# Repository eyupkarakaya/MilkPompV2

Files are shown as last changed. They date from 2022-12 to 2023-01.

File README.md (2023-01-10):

# Milk Pomp
Proje, kullanicinin farkli tip ve hacimli bardaklara makineden süt doldurmak için kullanilacak bir cihazin kontrol kartinin tasarlanmasi işidir.

Cihazın mekanik tasarımı, flow sensör ve pompa seçimi müşteri tarafından hazırlanmıştır. Bizim yapacağımız iş ise sistemin çalışmasını sağlayacak elektronik kontrol kartının tasarlanmasıdır.

## Sistemin Çalismasi
Cihaz maksimum 9 farklı bardak bilgisini hafızada tutabilir. Kullanıcı bardak seçimi yaparak kayıtlı bardak tiplerinden birini otomatik olarak doldurabilir. Fakat istenirse kayıtlı olmayan farklı bir kabı da manuel olarak istediği miktarda doldurabilir.

Cihaz üzerinde 3 adet buton ve 1 adet 7-Segment gösterge bulunmaktadır. Ayrıca, bir pulse girişi ile **Akış Sensoru** girişi okunacak ve çıkış olarak bir role kontrol edilecektir.

	* I/O (On/Off) butonu
	* Start butonu
	* Mode butonu
	* Akış Sensoru (Encoder Pulse Input)
	* Role
	
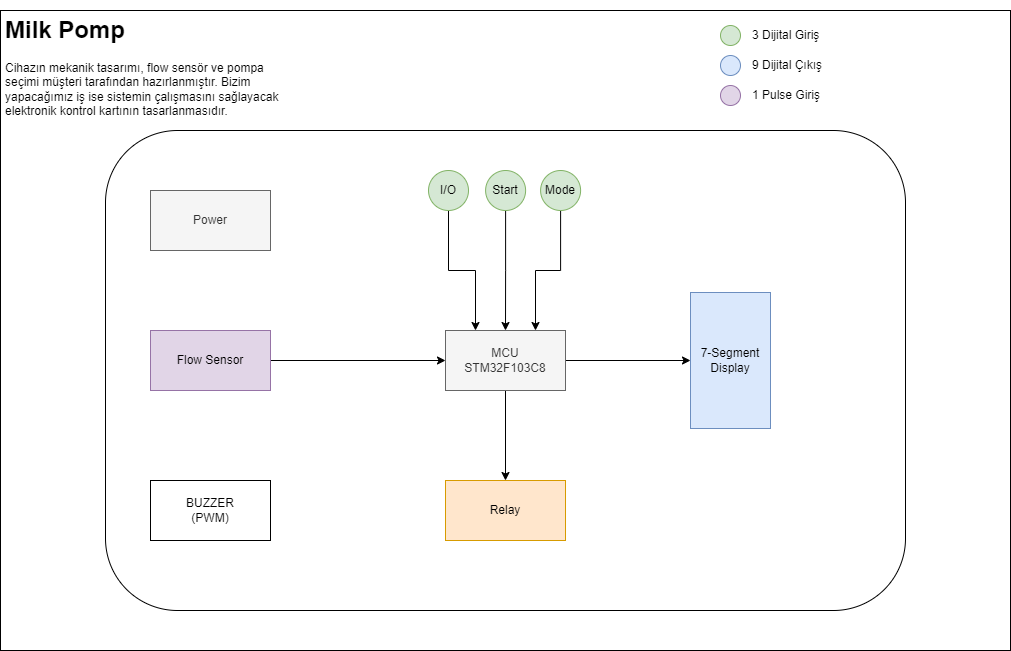
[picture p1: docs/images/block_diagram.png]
Block Diagram

	
Aşağıda tarif edilen çalışma şekilleri bu 3 buton ve gösterge kullanılarak gerçeklenecektir.

Sistemi çalıştırmak için I/O butonuna bir kere basıp bırakmak yeterlidir. Sistem kapalıyken gösterge ve diğer butonlar aktif değildir. I/O butonuna bir kere basılıp bırakıldığında sistem açılır, eğer kalibrasyon yapılmamışsa (hiç bardak tanımı yoksa) **C.** değeri görünür ve ekran yanıp söner. Aksi halde sabit olarak **0** yazar ve bardak seçimi için bekler.

Cihaz 3 farklı çalışma şekline sahip olacaktır.

### Kalibrasyon
Kalibrasyon modu, elimizde bulunan bardakların tanımlanması için kullanılır. Maksimum 9 farklı bardak tanımı yapılabilir.

Kalibrasyon modu bir adet bardak tanıtmak istenirse aşağıdaki algoritmaya göre çalışır

	1- Kalibrasyonu başlatmak için I/O butonuna 5 saniye basılı tutulur
	2- Gösterge 0 değerini gösterir ve nokta yanıp sönmeye başlar
	3- İstenilen bardak, cihazın bardak bölmesine yerleştirilir
	4- Mode butonu ile bardak seçimi yapılır (1, 2, 3, ..)
	5- Start butonuna basılı tutularak bardak doldurulur
	6- Bardak dolunca Start butonu bırakılır
	7- Start butonu bırakıldığında seçilen bardak ve doldurulan miktar bilgileri otomatik olarak kaydedilir
	8- Kalibrasyon modundan çıkmak için I/O butonuna 5 saniye bayunca basılır
	
Eğer birden fazla bardak tanımı yapılmak istenirse yukarıdaki algoritma basamaklarından 1 nolu adım ile kalibrasyon işlemi başlatılır. 2-7 adımları her bir bardak için tekrarlanır. Tüm bardakların tanımlanma işlemi bittiğinde 8 nolu adım ile kalibrasyon işlemi sonlandırılır.

Daha sonra tanımlı bir bardağın kalibrasyonu değiştirilmek istendiğinde veya yeni bir bardak tanımı yapılması gerektiğinde yukarıdaki algoritma tekrar uygulanabilir.

> Dikkat edilmesi gereken nokta, eğer bardak tanımları yapılmış bir cihazda tek bir bardağın kalibrasyonu değiştirlmek istenirse, Mode butonu ile doğru bardak numarasının seçildiğinden emin olunması gerekmektedir.

### Otomatik Mod
Kalibrasyonu yapılmış bir cihazda kullanıcı bardak seçimi yaparak tanımlı bardaklardan birini otomatik olarak doldurabilir.

	1- İstenilen bardak, cihazın bardak bölmesine yerleştirilir
	2- Mode butonu kullanılarak bardak seçimi yapılır
	3- Start butonuna basılıp bırakıldığında tanımlı miktar kadar dolum yapılır
	
Her bir bardak için yukarıdaki adımlar tekrarlanır.

### Manuel Mod
Kalibrasyon yapılarak tanımlanmamış bir bardak veya farklı bir kap doldurulmak istendiğinde Manuel mod kullanılır.

    1- Doldurulmak istenilen kap yerleştirilir.
	2- Start butonuna basılı tutulur. Butona basıldıktan 5 saniye sonra manuel dolum başlar
	3- Kullanıcı Start butonunu bıraktığında dolum işlemi sonlanır.

## Kaynak/Arastirmalar
- [Flow Sensor](https://www.hepsiburada.com/fluidotech-kahve-makinasi-pompasi-rotary-pompa-pirinc-govdeli-p-HBV000007SB1Q)
- [Flow Sensor Kullanimi](https://how2electronics.com/iot-water-flow-meter-using-esp8266-water-flow-sensor/)
- [ESP8266 With Water Flow Sensor](https://www.14core.com/wiring-esp8266-1212e-with-g12-liquid-water-flow-sensor-for-wireless-monitoring/)

## Kullanilacak Bilesenler
- [STM32G030F6P6TR](docs/DS12991.pdf) 
- [Relay](http://www.omron.com/ecb/products/pdf/en-g5le.pdf)
- [Display](https://docs.broadcom.com/docs/AV02-2553EN)
- [TLP291](https://toshiba.semicon-storage.com/info/docget.jsp?did=12884&prodName=TLP291)
- Buttons
- Buzzer 
- Resistors
- Capasitors
- Transistors
- Leds
## Algoritma Adimlari
    1) Basla
	2) I/O Butonuna bir kere basarak sistemi ac (Diger hersey pasif olmali)
	3) Eger Kalibrasyon yapilmamissa C.yanip soner once kalibrasyon yapilmali. Eger Kalibrasyon yapilmissa 14.adima git(ilk acilis icin gecerli)
	4) Kalibrasyonu başlatmak için I/O butonuna 5 saniye basılı tutulur
	5) Gösterge 0 değerini gösterir ve nokta yanıp sönmeye başlar
	6) İstenilen bardak, cihazın bardak bölmesine yerleştirilir
	7) Mode butonu ile bardak seçimi yapılır (1, 2, 3, ..)
	8) Start butonuna basılı tutularak bardak doldurulur
	9) Bardak dolunca Start butonu bırakılır
	10) Start butonu bırakıldığında seçilen bardak ve doldurulan miktar bilgileri otomatik olarak kaydedilir
	11) Kalibrasyon modundan çıkmak için I/O butonuna 5 saniye bayunca basılır
	12) Max 9 bardak tanimlanibilir, tanimlanma islemi bittikten sonra 11 adimla islem tamamlanir
	13) Eger birden fazla bardak tanimi yapilmak istenilirse 4 adimdan baslayip 5-11 arasi adimlar tekrarlanir
	14) Eger kalibrasyon yapilmissa ekranda 0 yazar ve bekler
	15) Iki farkli sekilde bardak doldurabilir otomatik ve manuel biri secilir
	16) Eger otomatik ise islem soyle devam eder
	17) İstenilen bardak, cihazın bardak bölmesine yerleştirilir
	18) Mode butonu kullanılarak bardak seçimi yapılır(ornek 1.bardak 0-100ml alir,2.bardak 200-300ml alir)
	19) Start butonuna basılıp bırakıldığında tanımlı miktar kadar dolum yapılır her bardak icin islem tekrar edilir
	20) Eger manuel ise oldurulmak istenilen kap yerleştirilir
	21) Start butonuna basılı tutulur. Butona basıldıktan 5 saniye sonra manuel dolum başlar
	22) Kullanıcı Start butonunu bıraktığında dolum işlemi sonlanır
   
## Algoritma Akış Şeması

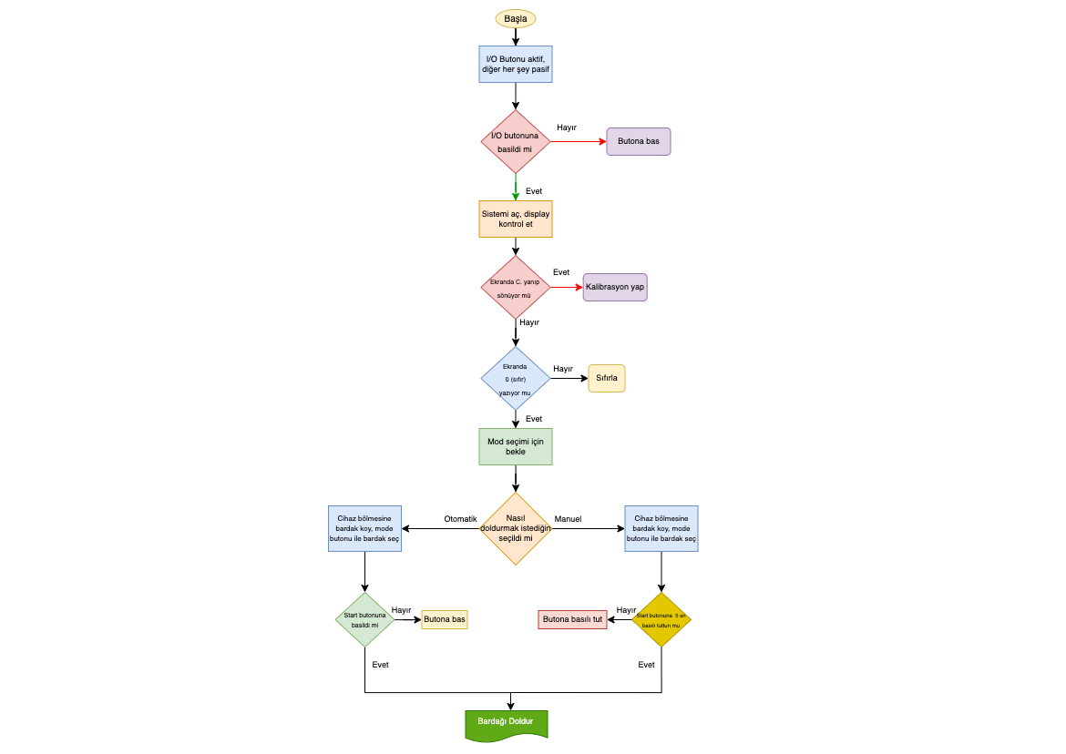
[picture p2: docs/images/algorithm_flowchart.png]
akış seması


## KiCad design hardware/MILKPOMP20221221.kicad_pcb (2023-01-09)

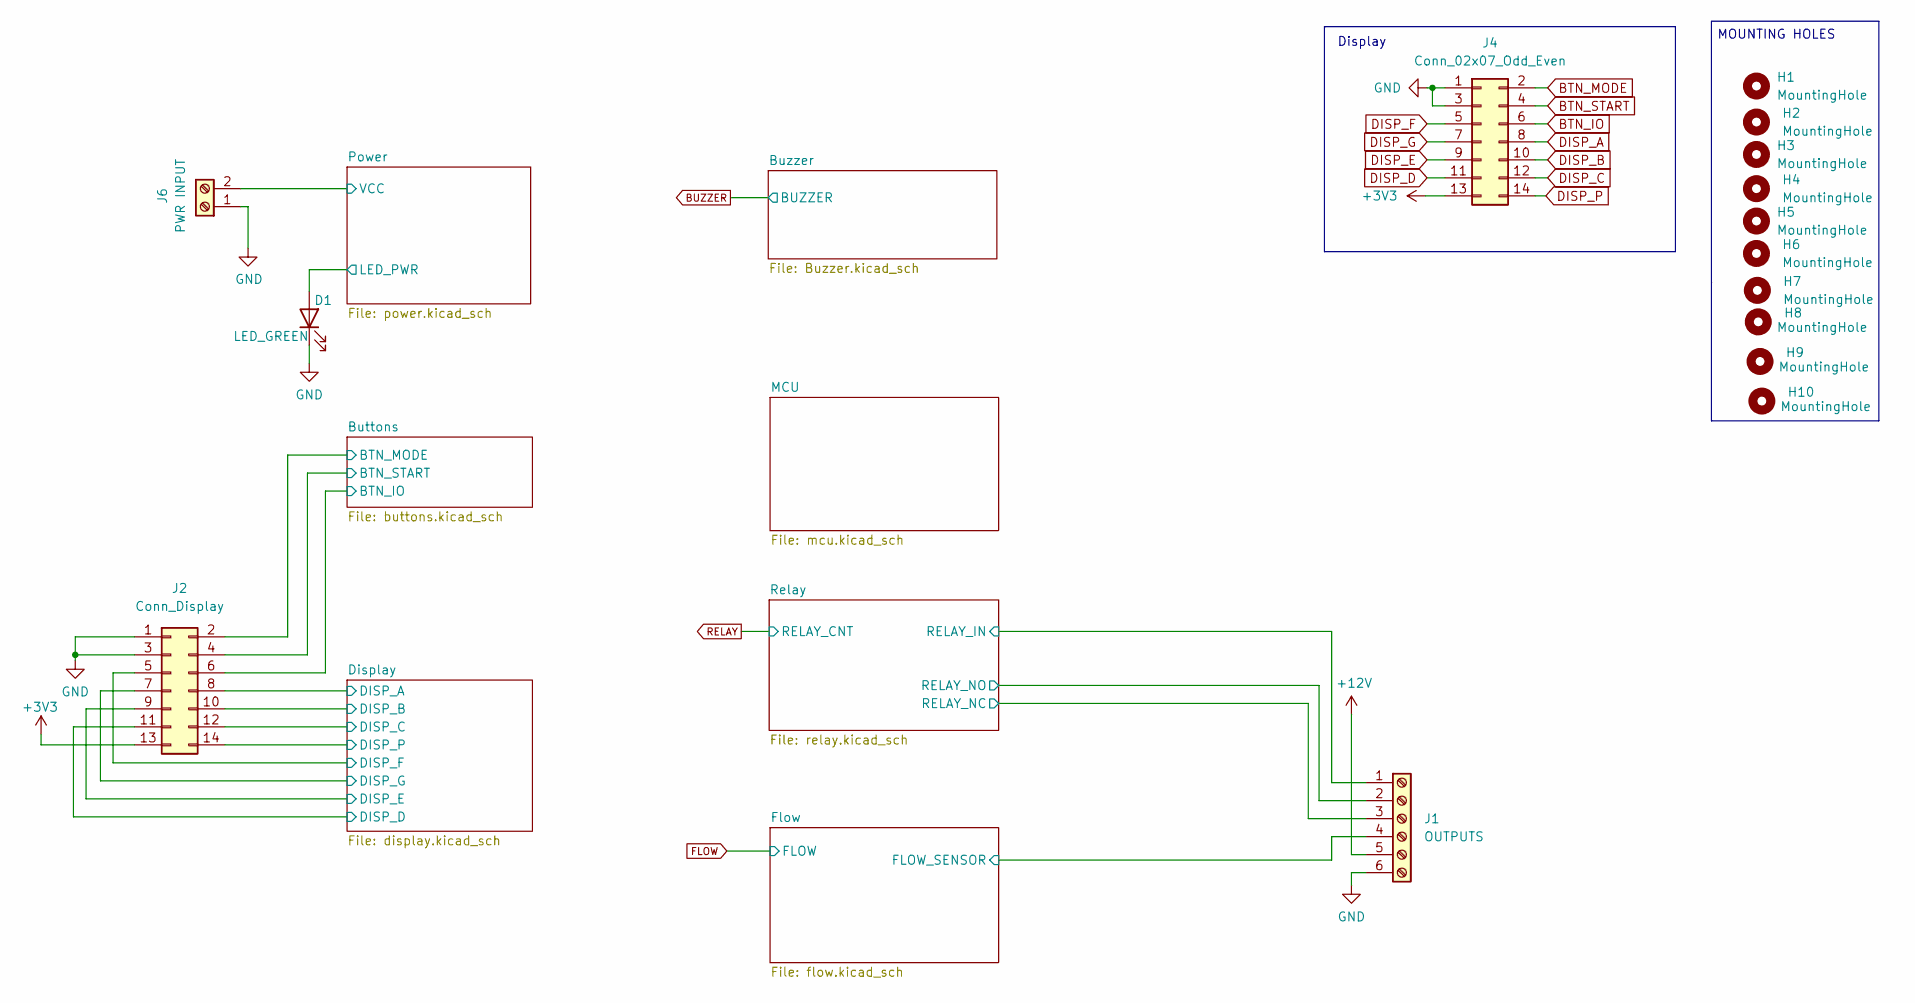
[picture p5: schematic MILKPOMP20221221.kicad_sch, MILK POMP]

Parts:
D1: LED_GREEN; LED_1206_3216Metric
H1, H2, H3, H4, H5, H6, H7, H8, H9, H10: MountingHole; MountingHole_2.5mm
J1: OUTPUTS; PhoenixContact_MSTBA_2,5_6-G-5,08_1x06_P5.08mm_Horizontal
J2: Conn_Display; Multicomp_MC9A12-1434_2x07x2.54mm_Straight
J4: Conn_02x07_Odd_Even; Multicomp_MC9A12-1434_2x07x2.54mm_Straight
J6: PWR INPUT; PhoenixContact_MSTBA_2,5_2-G_1x02_P5.00mm_Horizontal

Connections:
+3V3: J2.13, J4.13; also elsewhere on the board
+12V: J1.5, J6.2; also elsewhere on the board
/Buttons/BTN_IO: J2.6; also elsewhere on the board
/Buttons/BTN_MODE: J2.2; also elsewhere on the board
/Buttons/BTN_START: J2.4; also elsewhere on the board
/Display/DISP_A: J2.8; also elsewhere on the board
/Display/DISP_B: J2.10; also elsewhere on the board
/Display/DISP_C: J2.12; also elsewhere on the board
/Display/DISP_D: J2.11; also elsewhere on the board
/Display/DISP_E: J2.9; also elsewhere on the board
/Display/DISP_F: J2.5; also elsewhere on the board
/Display/DISP_G: J2.7; also elsewhere on the board
/Display/DISP_P: J2.14; also elsewhere on the board
/Flow/FLOW_SENSOR: J1.4; also elsewhere on the board
/Power/LED_PWR: D1.2 (A); also elsewhere on the board
/Relay /RELAY_IN: J1.1; also elsewhere on the board
/Relay /RELAY_NC: J1.3; also elsewhere on the board
/Relay /RELAY_NO: J1.2; also elsewhere on the board
BTN_IO: J4.6; also elsewhere on the board
BTN_MODE: J4.2; also elsewhere on the board
BTN_START: J4.4; also elsewhere on the board
DISP_A: J4.8; also elsewhere on the board
DISP_B: J4.10; also elsewhere on the board
DISP_C: J4.12; also elsewhere on the board
DISP_D: J4.11; also elsewhere on the board
DISP_E: J4.9; also elsewhere on the board
DISP_F: J4.5; also elsewhere on the board
DISP_G: J4.7; also elsewhere on the board
DISP_P: J4.14; also elsewhere on the board
GND: D1.1 (K), J1.6, J2.1, J2.3, J4.1, J4.3, J6.1; also elsewhere on the board

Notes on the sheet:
Display
MOUNTING HOLES

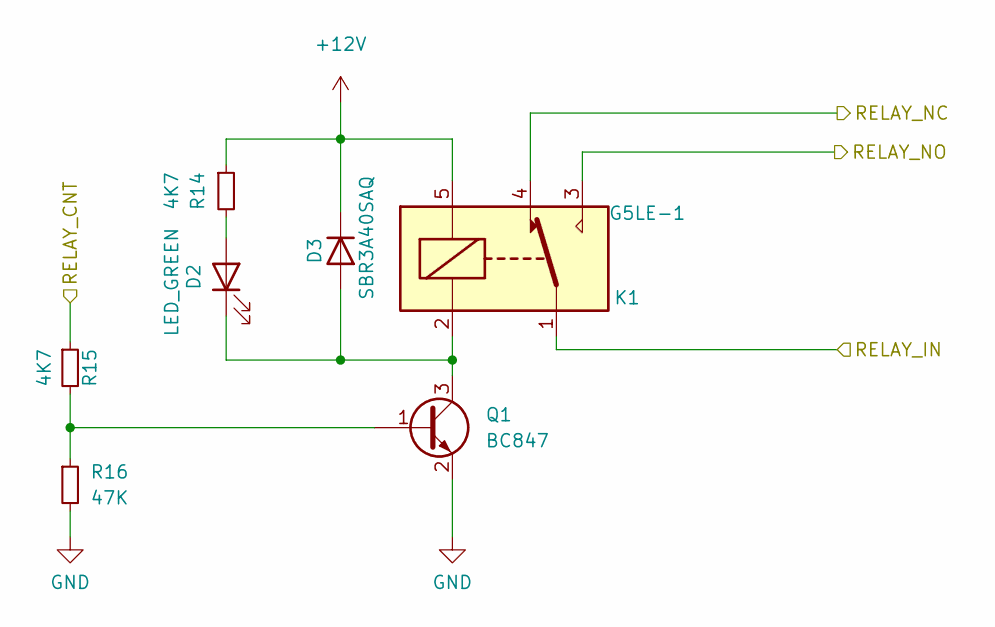
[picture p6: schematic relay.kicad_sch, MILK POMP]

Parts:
D2: LED_GREEN; LED_1206_3216Metric
D3: SBR3A40SAQ; D_SMB_Handsoldering; DIGIKEY_PART_NUMBER SBR3A40SAQ-13DICT-ND
K1: G5LE-1; Relay_SPDT_Omron-G5LE-1
Q1: BC847; SOT-23
R14, R15: 4K7; R_0603_1608Metric
R16: 47K; R_0603_1608Metric

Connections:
+12V: D3.1 (K), K1.5, R14.1; also elsewhere on the board
/Relay /RELAY_IN: K1.1; also elsewhere on the board
/Relay /RELAY_NC: K1.4; also elsewhere on the board
/Relay /RELAY_NO: K1.3; also elsewhere on the board
GND: Q1.2 (E), R16.2; also elsewhere on the board
unnamed: D2.1 (K), D3.2 (A), K1.2, Q1.3 (C)
unnamed: D2.2 (A), R14.2
unnamed: Q1.1 (B), R15.2, R16.1
RELAY: R15.1; also elsewhere on the board

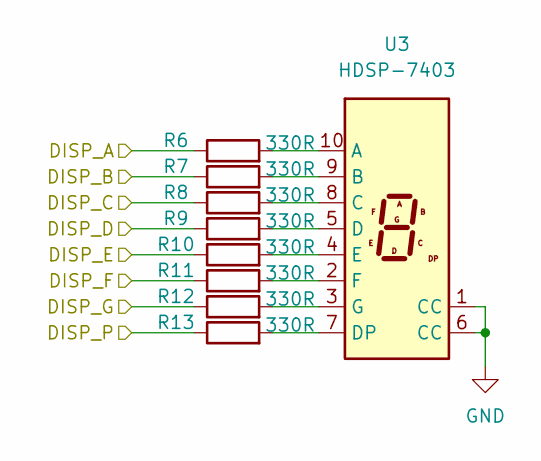
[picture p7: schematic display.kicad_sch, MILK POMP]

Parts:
R6, R7, R8, R9, R10, R11, R12, R13: 330R; R_0603_1608Metric
U3: HDSP-7403; HDSP-7401

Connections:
/Display/DISP_A: R6.1; also elsewhere on the board
/Display/DISP_B: R7.1; also elsewhere on the board
/Display/DISP_C: R8.1; also elsewhere on the board
/Display/DISP_D: R9.1; also elsewhere on the board
/Display/DISP_E: R10.1; also elsewhere on the board
/Display/DISP_F: R11.1; also elsewhere on the board
/Display/DISP_G: R12.1; also elsewhere on the board
/Display/DISP_P: R13.1; also elsewhere on the board
GND: U3.1 (CC), U3.6 (CC); also elsewhere on the board
unnamed: R6.2, U3.10 (A)
unnamed: R7.2, U3.9 (B)
unnamed: R8.2, U3.8 (C)
unnamed: R9.2, U3.5 (D)
unnamed: R10.2, U3.4 (E)
unnamed: R11.2, U3.2 (F)
unnamed: R12.2, U3.3 (G)
unnamed: R13.2, U3.7 (DP)

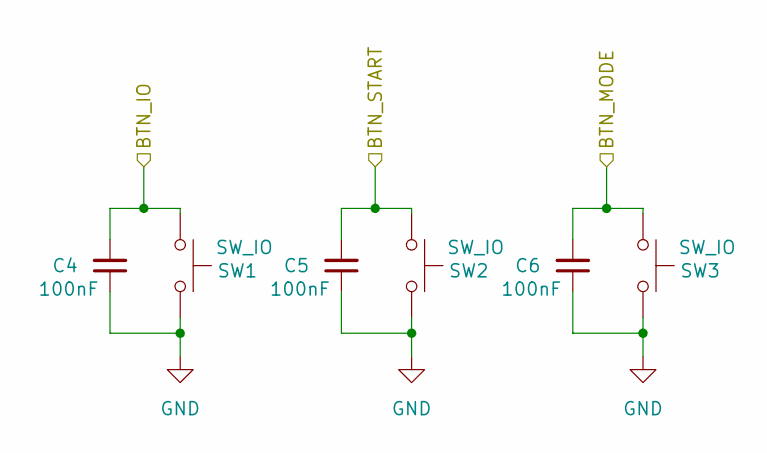
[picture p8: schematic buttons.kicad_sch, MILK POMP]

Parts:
C4, C5, C6: 100nF; C_0603_1608Metric
SW1, SW2, SW3: SW_IO; SW_PUSH-12mm

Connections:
/Buttons/BTN_IO: C4.2, SW1.1; also elsewhere on the board
/Buttons/BTN_MODE: C6.2, SW3.1; also elsewhere on the board
/Buttons/BTN_START: C5.2, SW2.1; also elsewhere on the board
GND: C4.1, C5.1, C6.1, SW1.2, SW2.2, SW3.2; also elsewhere on the board

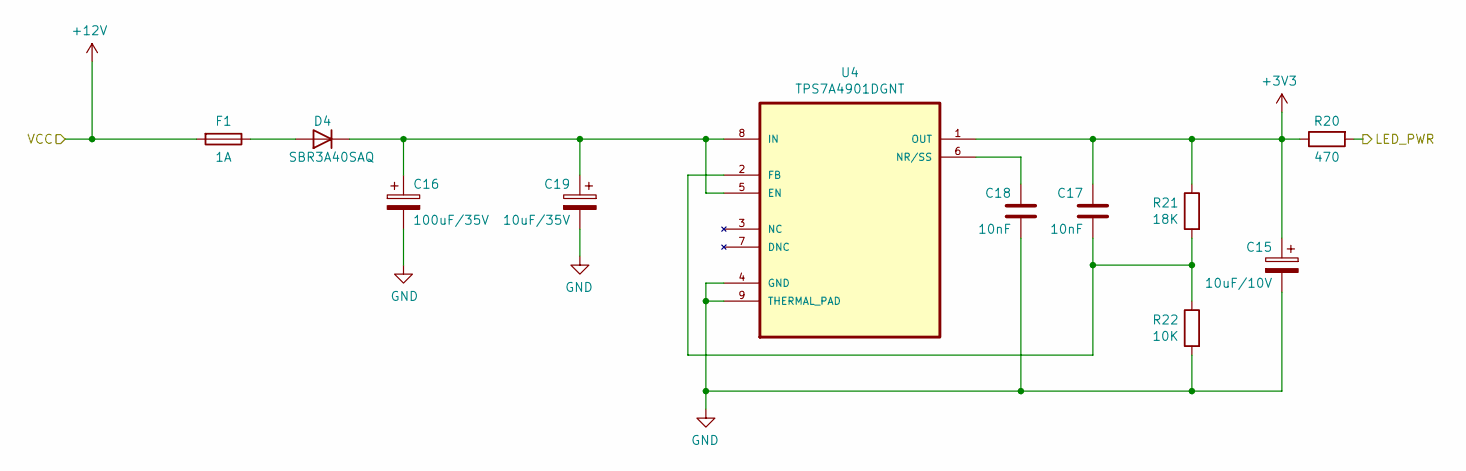
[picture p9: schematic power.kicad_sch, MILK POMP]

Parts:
C15: 10uF/10V; CP_Elec_6.3x7.7; Digikey 10-EEE-FN1A100RDKR-ND
C16: 100uF/35V; CP_Elec_10x10.5; Digikey PCE3951TR-ND
C17, C18: 10nF; C_0603_1608Metric; Digikey 1276-CL10B103KB8WPJCDKR-ND
C19: 10uF/35V; CP_Elec_6.3x7.7; Digikey 10-EEE-FN1A100RDKR-ND
D4: SBR3A40SAQ; D_SMB_Handsoldering; DIGIKEY_PART_NUMBER SBR3A40SAQ-13DICT-ND
F1: 1A; Fuse_1206_3216Metric; Digikey F2881CT-ND
R20: 470; R_0603_1608Metric; Digikey YAG1301DKR-ND
R21: 18K; R_0603_1608Metric; Digikey YAG3570DKR-ND
R22: 10K; R_0603_1608Metric; Digikey 311-10.0KHRDKR-ND
U4: TPS7A4901DGNT; SOP65P490X110-9N; MPN TPS7A4901DGNT; Digikey 296-27769-6-ND

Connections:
+3V3: C15.1, C17.1, R20.1, R21.1, U4.1 (OUT); also elsewhere on the board
+12V: F1.2; also elsewhere on the board
/Power/LED_PWR: R20.2; also elsewhere on the board
GND: C15.2, C16.2, C18.2, C19.2, R22.2, U4.4 (GND), U4.9 (THERMAL_PAD); also elsewhere on the board
unnamed: C16.1, C19.1, D4.1 (K), U4.5 (EN), U4.8 (IN)
unnamed: C17.2, R21.2, R22.1, U4.2 (FB)
unnamed: C18.1, U4.6 (NR/SS)
unnamed: D4.2 (A), F1.1

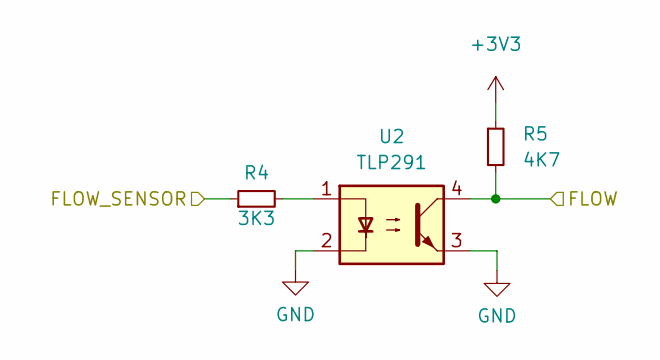
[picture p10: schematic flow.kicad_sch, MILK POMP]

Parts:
R4: 3K3; R_0603_1608Metric
R5: 4K7; R_0603_1608Metric
U2: TLP291; SOIC-4_4.55x2.6mm_P1.27mm

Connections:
+3V3: R5.1; also elsewhere on the board
/Flow/FLOW_SENSOR: R4.1; also elsewhere on the board
FLOW: R5.2, U2.4; also elsewhere on the board
GND: U2.2, U2.3; also elsewhere on the board
unnamed: R4.2, U2.1

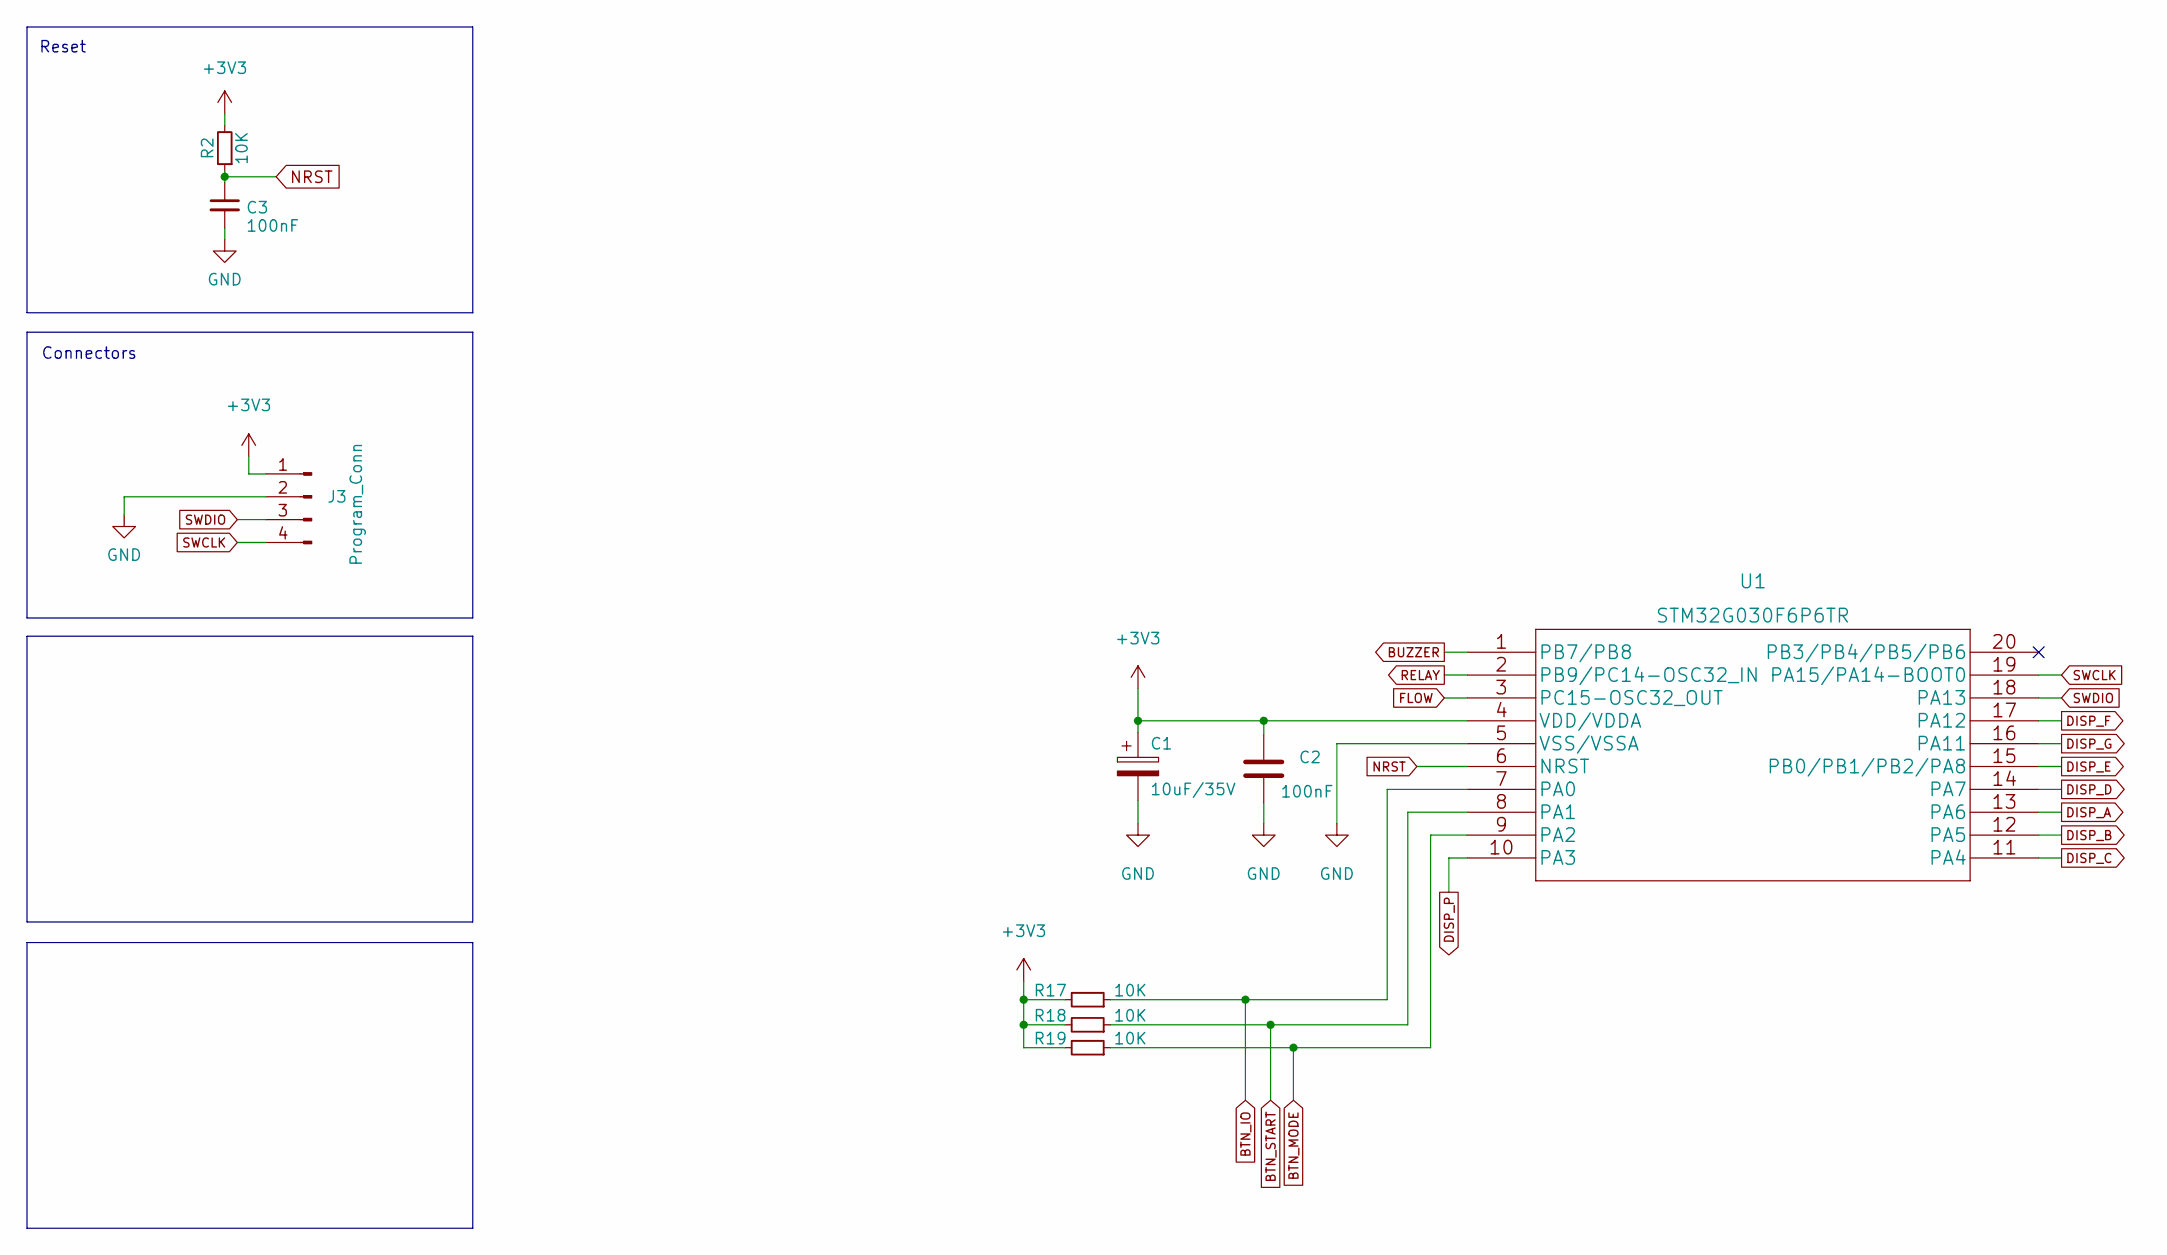
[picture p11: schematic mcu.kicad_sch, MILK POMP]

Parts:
C1: 10uF/35V; CP_Elec_6.3x7.7; Digikey 10-EEE-FN1A100RDKR-ND
C2: 100nF; C_0603_1608Metric; Digikey AC0603KPX7R7BB104
C3: 100nF; C_0603_1608Metric
J3: Program_Conn; PinHeader_1x04_P2.54mm_Vertical
R2, R17, R18, R19: 10K; R_0603_1608Metric
U1: STM32G030F6P6TR; SOP65P640X120-20N

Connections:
+3V3: C1.1, C2.1, J3.1, R2.2, R17.2, R18.2, R19.2, U1.4 (VDD/VDDA); also elsewhere on the board
BTN_IO: R17.1, U1.7 (PA0); also elsewhere on the board
BTN_MODE: R19.1, U1.9 (PA2); also elsewhere on the board
BTN_START: R18.1, U1.8 (PA1); also elsewhere on the board
BUZZER: U1.1 (PB7/PB8); also elsewhere on the board
DISP_A: U1.13 (PA6); also elsewhere on the board
DISP_B: U1.12 (PA5); also elsewhere on the board
DISP_C: U1.11 (PA4); also elsewhere on the board
DISP_D: U1.14 (PA7); also elsewhere on the board
DISP_E: U1.15 (PB0/PB1/PB2/PA8); also elsewhere on the board
DISP_F: U1.17 (PA12); also elsewhere on the board
DISP_G: U1.16 (PA11); also elsewhere on the board
DISP_P: U1.10 (PA3); also elsewhere on the board
FLOW: U1.3 (PC15-OSC32_OUT); also elsewhere on the board
GND: C1.2, C2.2, C3.2, J3.2, U1.5 (VSS/VSSA); also elsewhere on the board
NRST: C3.1, R2.1, U1.6 (NRST)
RELAY: U1.2 (PB9/PC14-OSC32_IN); also elsewhere on the board
SWCLK: J3.4, U1.19 (PA15/PA14-BOOT0)
SWDIO: J3.3, U1.18 (PA13)

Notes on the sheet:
Connectors
Reset

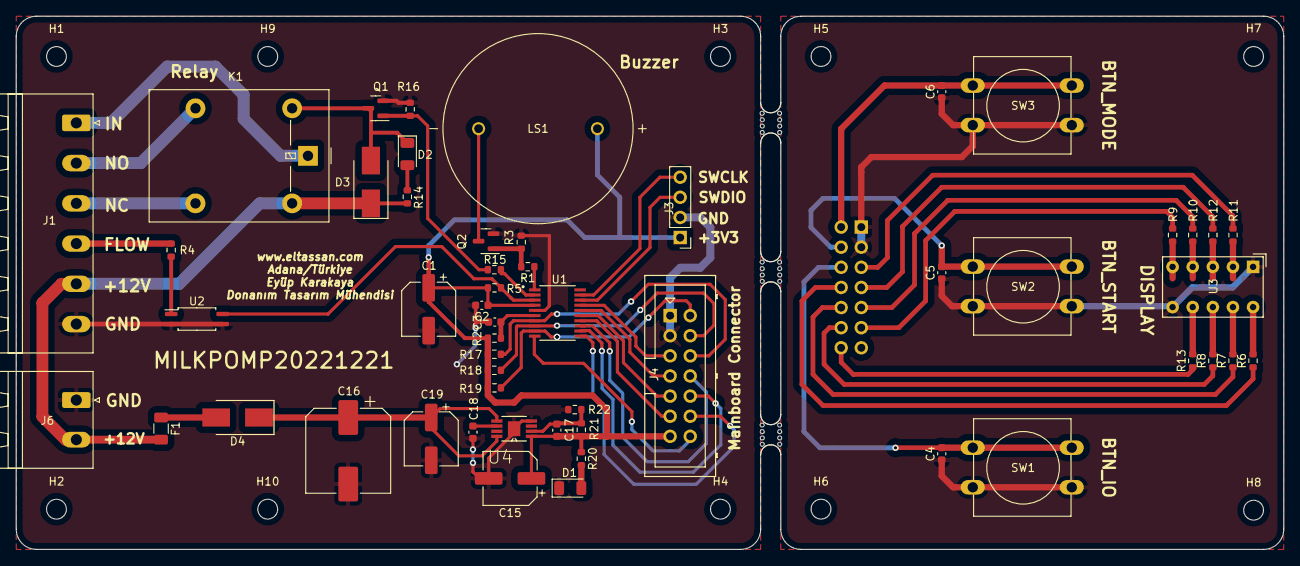
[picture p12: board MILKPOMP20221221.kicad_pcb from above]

Board: 2 copper layers, 160.0 x 67.3 mm, 67 parts (1 on the bottom side), 54 nets.

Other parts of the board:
LS1: KPEG228; XDCR_KPEG228
Q2: BC847; SOT-23
R1: 4K7; R_0603_1608Metric
R3: 47K; R_0603_1608Metric
mouse-bite-2.54mm-slot, mouse-bite-2.54mm-slot#2, mouse-bite-2.54mm-slot#3: VAL**; mouse-bite-2.54mm-slot

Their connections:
+3V3: LS1.P; also elsewhere on the board
BUZZER: R1.1; also elsewhere on the board
GND: Q2.2 (E), R3.2; also elsewhere on the board
unnamed: LS1.N, Q2.3 (C)
unnamed: Q2.1 (B), R1.2, R3.1

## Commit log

2022-12-05 second commit
    [MilkPompV2.kicad_pcb]
2022-12-05 project name added
    [MilkPompV2.kicad_pcb]
2022-12-05 PCB arranged
    [MilkPompV2.kicad_pcb]
2022-12-05 Readme file changed
    [MilkPompV2.kicad_pcb, MilkPompV2.kicad_sch]
2022-12-05 naming is complete
    [MilkPompV2.kicad_pcb]
2022-12-05 gerber files chanced
    [MilkPompV2-B_Cu.gbl, MilkPompV2-B_Mask.gbs, MilkPompV2-B_Paste.gbp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]
2022-12-06 arrangement has been made
    [MilkPompV2-B_Cu.gbl, MilkPompV2-B_Mask.gbs, MilkPompV2-B_Paste.gbp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]
2023-01-09 name stardandi added, readme file updated
    [MILKPOMP20221221.kicad_pcb, MILKPOMP20221221.kicad_sch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]
2023-01-10 flow chart added
    [buttons.kicad_sch, mcu.kicad_sch]
